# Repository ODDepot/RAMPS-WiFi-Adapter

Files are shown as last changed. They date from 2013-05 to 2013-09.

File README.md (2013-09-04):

The RAMPS WiFi Adapter provides wireless networking for RepRap's RAMPS (Arduino Mega Pololu Shield) controller.

### News

#### 9/4/2013
Version 0.2 has been tested and is functional. Further work on setup.ino and setup.py is needed for a friendly configuration process. Higher baudrates may be achieved but have not been fully tested.

#### 6/19/2013
Version 0.2 is ready to be ordered and tested. The LM358DMR2G is replacing the TLV2452CDGKR and voltage dividers are being added along with a pullup and pulldown resistor. The first version has some errors. Overdriving the TLV2452CDGKR inputs at 5V with 3.3V supply is not possible. Replacing it with a LM358DMR2G works, however, a pullup resistor for RESET and a pulldown resistor for GPIO9 on the RN-171 is needed whenever jumpers are not connected. Besides these issues, Version 0.1 is able to connect and send data. The antenna appears very capable.

#### 5/13/2013
Boards for the first version have been ordered and testing will begin soon.

### Setup

#### Using Marlin firmware and Pronterface host software
Make sure the RAMPS WiFi Adapter is installed correctly on RAMPS and the Reset and Default pin jumpers are in place. Upload setup.ino to the Arduino Mega with your custom settings. Observe output from the RN171 (WiFi module onboard the adapter) with the Arduino IDE Serial Monitor. If the RN171 successful assoicates with your wireless network, the RN171 should provide an IP Address and the only LED blinking should be green. Verify this by checking your router. Also, you may want to configure your router for Static DHCP so that it always leases the same IP Address for the same MAC Address (on the RN171).

In Configuration.h of Marlin, change '#define SERIAL_PORT 0' to '#define SERIAL_PORT 2' and change '#define BAUDRATE 250000' to '#define BAUDRATE 9600', then upload. Remove the Reset and Default pin jumpers and reset RAMPS. Wait a few seconds. In Pronterface, type [IP Address]:2000 into the 'Port' bar (for example, 192.168.1.100:2000), then connect.

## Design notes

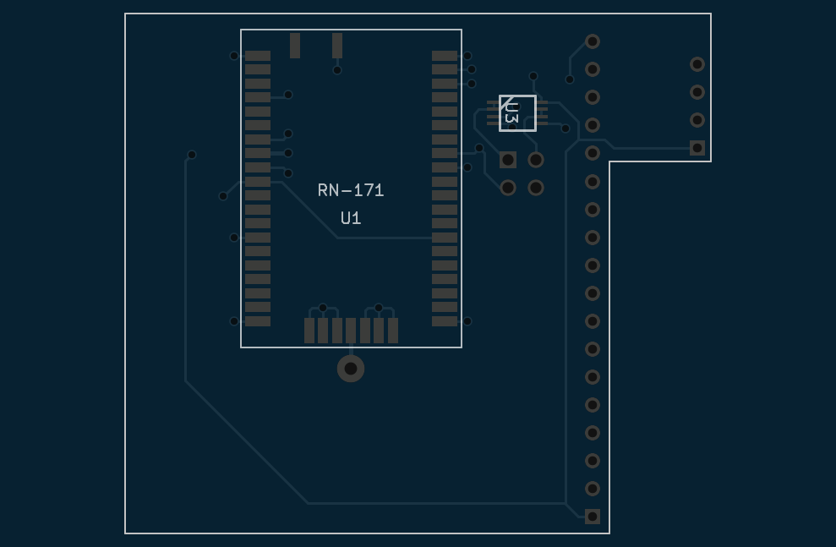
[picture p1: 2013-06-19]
rev-0.2/back.png

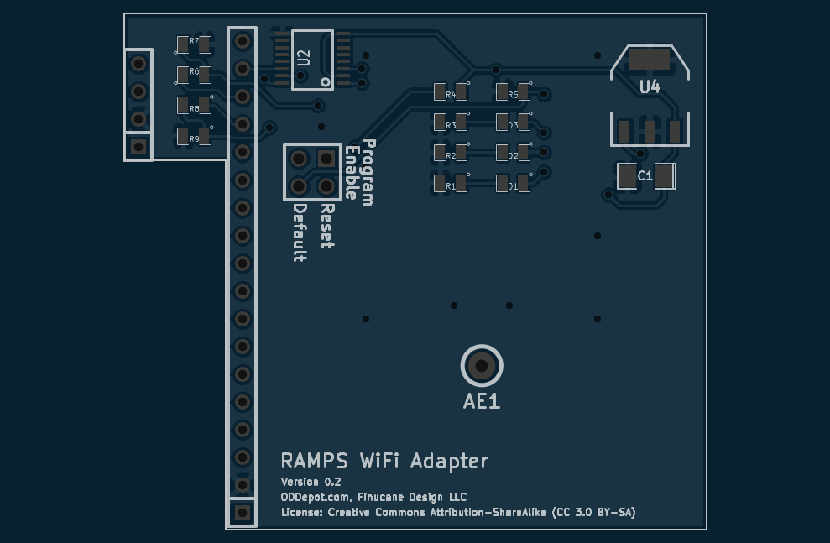
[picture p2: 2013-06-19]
rev-0.2/front.png

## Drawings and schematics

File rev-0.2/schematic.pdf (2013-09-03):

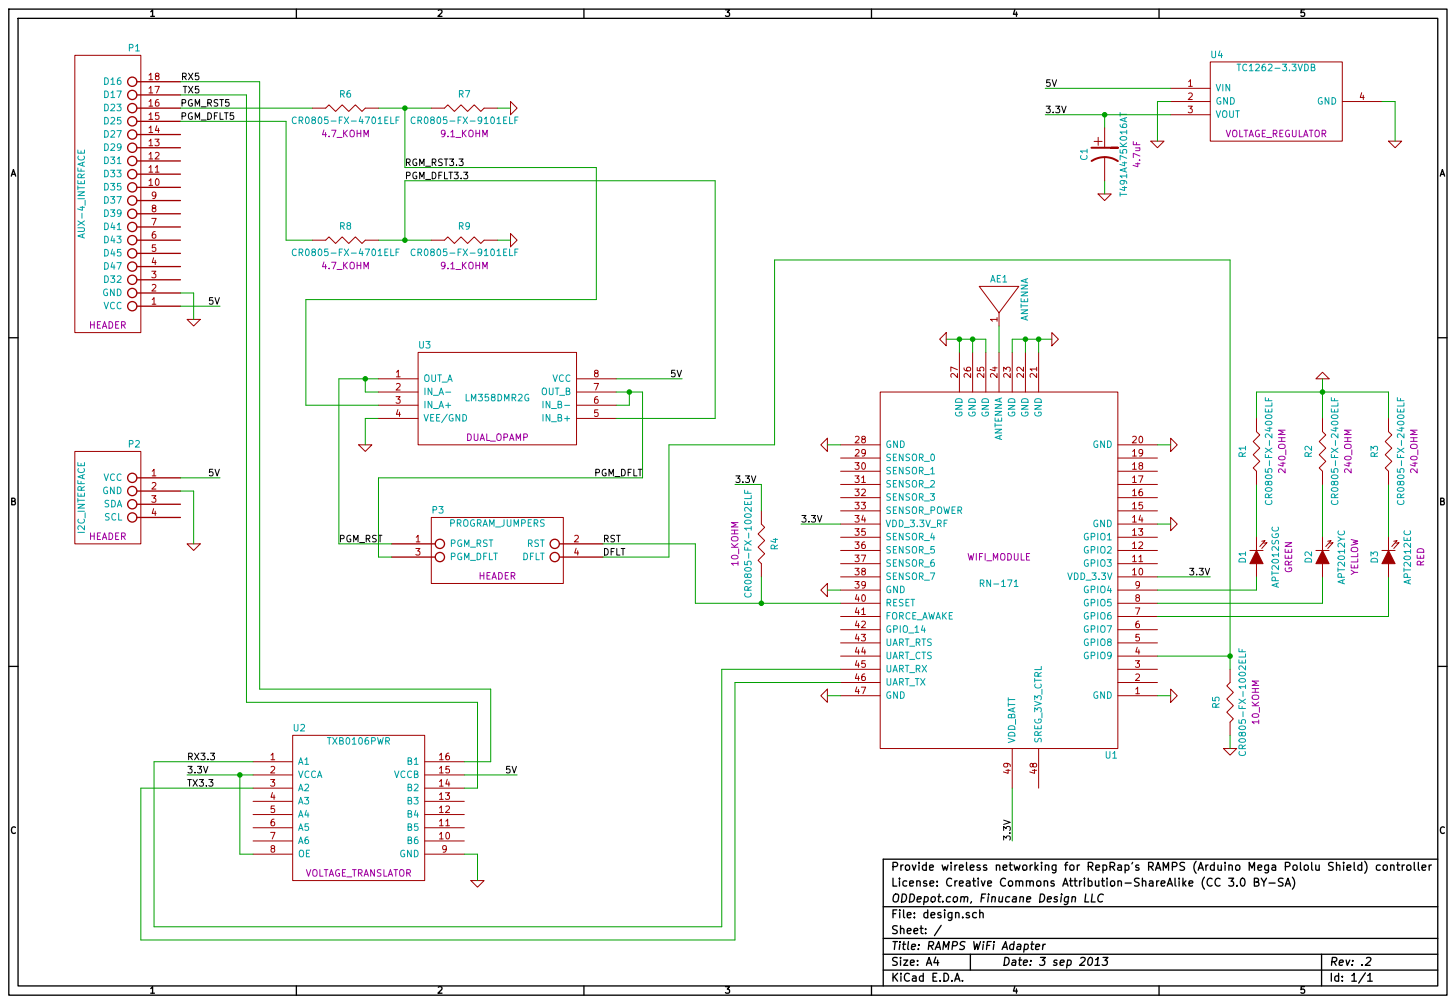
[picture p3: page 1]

Provide wireless networking for RepRap's RAMPS (Arduino Mega Pololu Shield) controller
License: Creative Commons Attribution-ShareAlike (CC 3.0 BY-SA)
ODDepot.com, Finucane Design LLC
File: design.sch
Sheet: /
Title: RAMPS WiFi Adapter
KiCad E.D.A.

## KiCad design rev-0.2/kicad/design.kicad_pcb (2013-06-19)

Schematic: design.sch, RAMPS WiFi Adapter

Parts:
AE1: ANTENNA
C1: T491A475K016AT
D1: APT2012SGC
D2: APT2012YC
D3: APT2012EC
P1: AUX-4_INTERFACE
P2: I2C_INTERFACE
P3: PROGRAM_JUMPERS
R1, R2, R3: CR0805-FX-2400ELF
R4, R5: CR0805-FX-1002ELF
R6, R8: CR0805-FX-4702ELF
R7, R9: CR0805-FX-9102ELF
U1: RN-171
U2: TXB0106PWR
U3: LM358DMR2G
U4: TC1262-3.3VDB

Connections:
/3.3V: C1.1, R4.1, U1.10 (VDD_3.3V), U1.34 (VDD_3.3V_RF), U1.49 (VDD_BATT), U2.2 (VCCA), U2.8 (OE), U4.3 (VOUT)
/5V: P1.1, P2.1, U2.15 (VCCB), U3.8 (VCC), U4.1 (VIN)
/DFLT: P3.4 (DFLT), R5.1, U1.4 (GPIO9)
/PGM_DFLT: P3.3 (PGM_DFLT), U3.6 (IN_B-), U3.7 (OUT_B)
/PGM_DFLT3.3: R8.2, R9.1, U3.5 (IN_B+)
/PGM_DFLT5: P1.15, R8.1
/PGM_RST: P3.1 (PGM_RST), U3.1 (OUT_A), U3.2 (IN_A-)
/PGM_RST5: P1.16, R6.1
/RGM_RST3.3: R6.2, R7.1, U3.3 (IN_A+)
/RST: P3.2 (RST), R4.2, U1.40 (RESET)
/RX3.3: U1.45 (UART_RX), U2.1 (A1)
/RX5: P1.18, U2.16 (B1)
/TX3.3: U1.46 (UART_TX), U2.3 (A2)
/TX5: P1.17, U2.14 (B2)
GND: C1.2, P1.2, P2.2, R1.2, R2.2, R3.2, R5.2, R7.2, R9.2, U1.1 (GND), U1.14 (GND), U1.20 (GND), U1.21 (GND), U1.22 (GND), U1.23 (GND), U1.25 (GND), U1.26 (GND), U1.27 (GND), U1.28 (GND), U1.39 (GND), U1.47 (GND), U2.9 (GND), U3.4 (VEE/GND), U4.2 (GND), U4.4 (GND)
unnamed: D1.1 (AN), U1.9 (GPIO4)
unnamed: D3.2 (CA), R3.1
unnamed: D2.2 (CA), R2.1
unnamed: D1.2 (CA), R1.1
unnamed: D3.1 (AN), U1.7 (GPIO6)
unnamed: AE1.1, U1.24 (ANTENNA)
unnamed: D2.1 (AN), U1.8 (GPIO5)

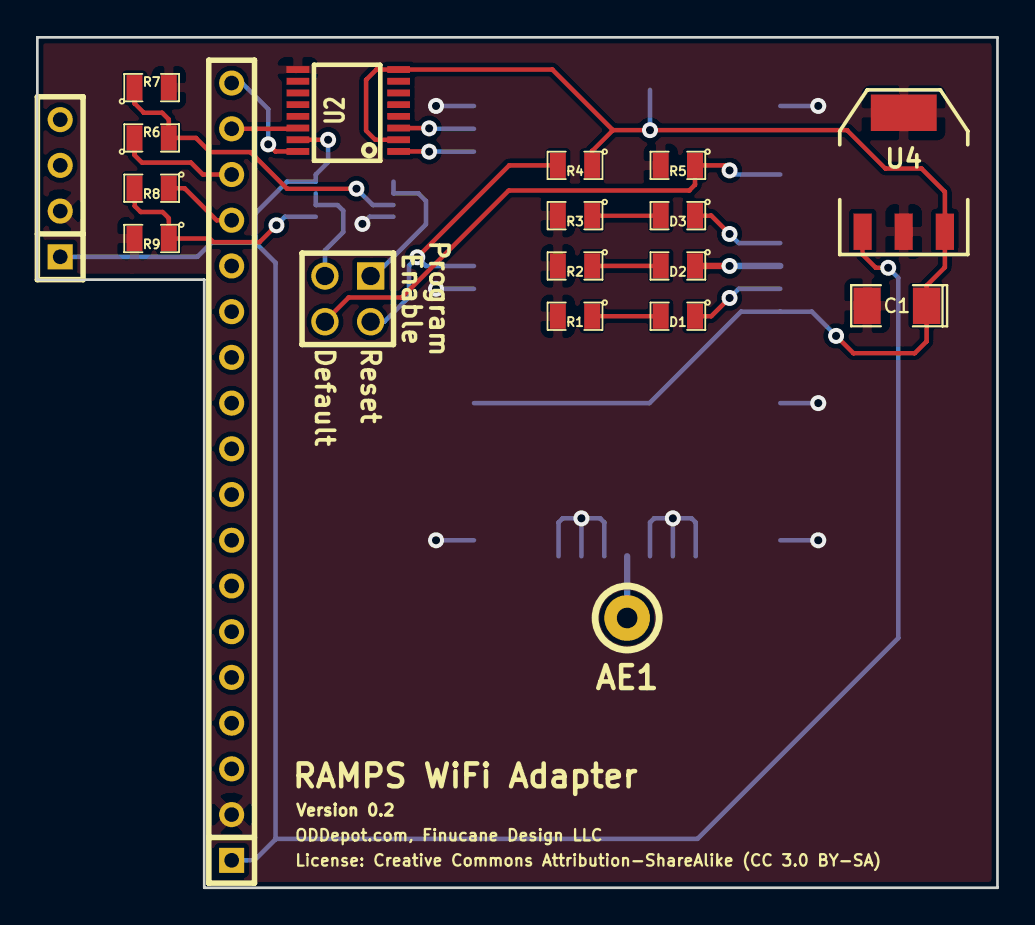
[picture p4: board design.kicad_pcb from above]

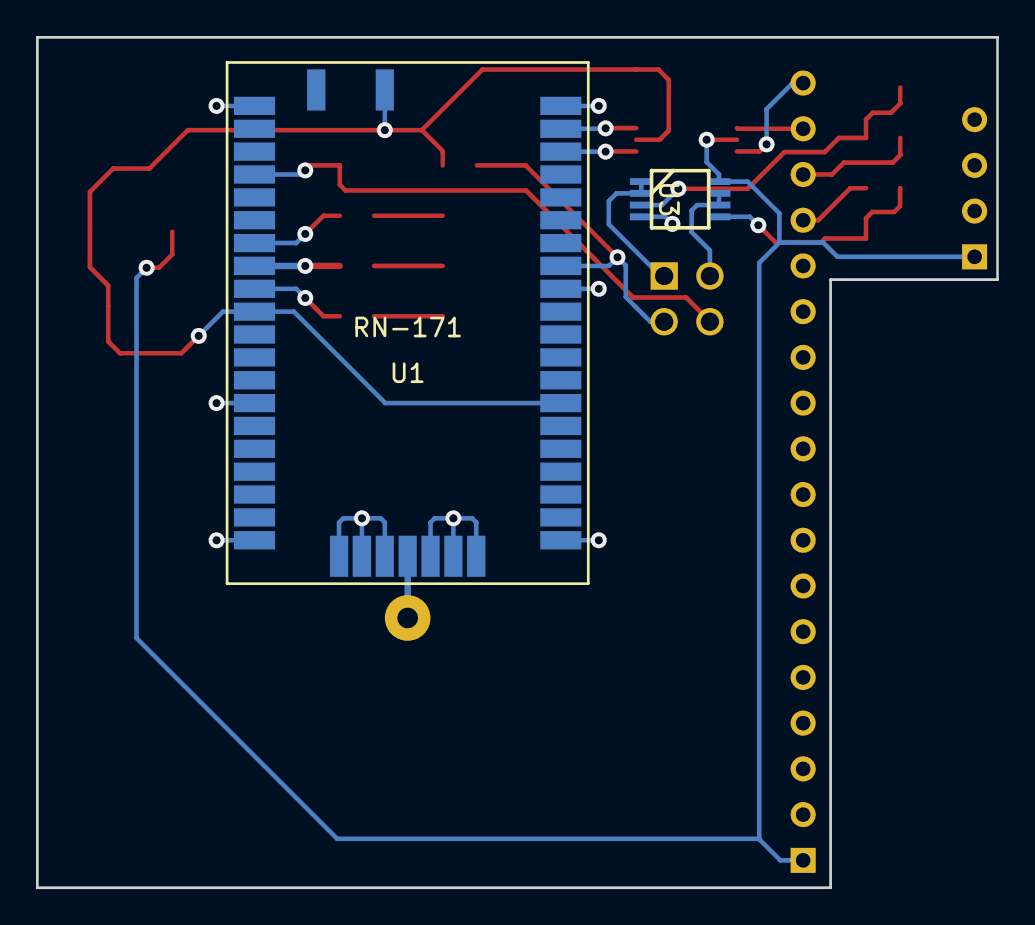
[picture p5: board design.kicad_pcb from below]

Board: 2 copper layers, 53.3 x 47.2 mm, 21 parts (2 on the bottom side), 22 nets.

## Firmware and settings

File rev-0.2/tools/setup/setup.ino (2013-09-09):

// This sketch configures the RN171 on the RAMPS WiFi Adapter. If successful, the RN171 will
// associate with your wireless network. Use the Arduino IDE Serial Monitor to observe output.
// Modify the following settings for your router. Make sure the Reset and Default pin jumpers are
// in place!

//////////////////////////////////////////////////
// Modify these settings to connect to your router
// Make sure they are exact! Double check!
//////////////////////////////////////////////////

// Type your router name here
String SSID = "My_SSID";

// Type your passphrase here
String Passphrase = "My_Passphrase";

// Uncomment ONE of the following security types...
//int Auth_Type = 0; // Open
int Auth_Type = 2; // WPA2
//int Auth_Type = 3; // WPA1
//int Auth_Type = 4; // Mixed

//////////////////////////////////////////////////
//////////////////////////////////////////////////
//////////////////////////////////////////////////

// Configuration settings for the RN171
long baud_rate = 115200;  // The baud rate between the RN171 and Mega, this must match the baud rate set in Marlin
String device_id = "RAMPS WiFi Adapter";  // If using more than one adapter, each device_id should be unique

int RST = 23;
int DFLT = 25;

const int command_buffer_size = 64;
char command[command_buffer_size];


void establish_comm() {
  Serial.begin(9600);
  Serial2.begin(9600);
}

void send_command(String str_command) {
  if (str_command != "$$$") {
      str_command += "\r\n";
  }
  str_command.toCharArray(command, command_buffer_size);
  Serial2.write(command);
}

void print_response() {
  delay(1000);
  while (Serial2.available() > 0) {
    Serial.write(Serial2.read());
  }
  Serial.write("\r\n");
}

void clear_receive_buffer() {
  delay(1000);
  while (Serial2.available() > 0) {
    Serial2.read();
  }
}

String escape_space(String string) {

  string.replace(" ", "$");
  return string;
}

void setup() {
  pinMode(RST, OUTPUT);
  pinMode(DFLT, OUTPUT);

  // The following write sequence restores the RN171 to factory defaults
  digitalWrite(DFLT, HIGH);
  delay(1000);
  digitalWrite(RST, LOW);
  delay(1000);
  digitalWrite(RST, HIGH);
  delay(1000);
  digitalWrite(DFLT, LOW);
  delay(1000);
  digitalWrite(DFLT, HIGH);
  delay(1000);
  digitalWrite(DFLT, LOW);
  delay(1000);
  digitalWrite(DFLT, HIGH);
  delay(1000);
  digitalWrite(DFLT, LOW);
  delay(1000);
  digitalWrite(DFLT, HIGH);
  delay(1000);
  digitalWrite(DFLT, LOW);
  delay(1000);
  digitalWrite(DFLT, HIGH);
  delay(1000);
  digitalWrite(DFLT, LOW);
  delay(1000);
  digitalWrite(DFLT, HIGH);
  delay(1000);
  digitalWrite(DFLT, LOW);
  delay(1000);

  // Reset the RN171
  digitalWrite(RST, LOW);
  delay(1000);
  digitalWrite(RST, HIGH);
  delay(1000);

  establish_comm();

  send_command("$$$");
  print_response();

  send_command("");  // A "hiccup" sometimes returns an error for the first commmand after "$$$", so send this and ignore response
  clear_receive_buffer();

  send_command(String(("set option device_id ") + escape_space(device_id)));
  print_response();
  
  send_command((String("set wlan ssid ") + escape_space(SSID)));
  print_response();

  send_command((String("set wlan auth ") + Auth_Type));
  print_response();

  send_command((String("set wlan phrase ") + escape_space(Passphrase)));
  print_response();

  send_command("set wlan linkmon 0");  // WiFly de-authenticates and re-authenticates continously with the AP when this is > 0, not sure why...
  print_response();
  
  send_command("set wlan join 1");
  print_response();
  
  send_command("set ip dhcp 1");
  print_response();

  send_command((String("set uart baud ") + baud_rate));
  print_response();

  send_command("save");
  print_response();
  
  // Reset the RN171 again
  digitalWrite(RST, LOW);
  delay(1000);
  digitalWrite(RST, HIGH);
  delay(1000);
}

void loop() {
}

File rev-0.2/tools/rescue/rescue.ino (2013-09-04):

// This sketch restores the RN171 on the RAMPS WiFi Adapter to factory defaults. Try this if the
// RN171 becomes unresponsive, then use debug.ino. Make sure the Reset and Default pin jumpers
// are in place! See the RN171-EK datasheet for "factory reset" sequence
// (http://www.rovingnetworks.com/resources/download/147/RN_171_EK_Data_Sheet).


int RST = 23;
int DFLT = 25;


void setup() {
  pinMode(RST, OUTPUT);
  pinMode(DFLT, OUTPUT);

  // The following write sequence restores the RN171 to factory defaults
  // Make sure the Reset and Default pin jumpers are in place!
  digitalWrite(DFLT, HIGH);
  delay(1000);
  digitalWrite(RST, LOW);
  delay(1000);
  digitalWrite(RST, HIGH);
  delay(1000);
  digitalWrite(DFLT, LOW);
  delay(1000);
  digitalWrite(DFLT, HIGH);
  delay(1000);
  digitalWrite(DFLT, LOW);
  delay(1000);
  digitalWrite(DFLT, HIGH);
  delay(1000);
  digitalWrite(DFLT, LOW);
  delay(1000);
  digitalWrite(DFLT, HIGH);
  delay(1000);
  digitalWrite(DFLT, LOW);
  delay(1000);
  digitalWrite(DFLT, HIGH);
  delay(1000);
  digitalWrite(DFLT, LOW);
  delay(1000);
  digitalWrite(DFLT, HIGH);
  delay(1000);
  digitalWrite(DFLT, LOW);
}

void loop() {
}

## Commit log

2013-05-13 Intial commit for rev-0.1, README.md, and LICENSE.md
    [design.kicad_pcb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]
2013-05-14 Create Mouser BOM
    [mouser_bom.csv]
2013-06-07 Generate solder paste gerber files
    [design-B_Paste.gbp, design-F_Paste.gtp]
2013-06-19 Adding rev-0.2 which corrects some errors with rev-0.1 (see README). Also adding some some tools (still a work in progress) for configuring the RN-171.
    [design-B_Cu.gbl, design-B_Mask.gbs, design-B_Paste.gbp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]
2013-09-03 Changing R6,R8 to 4.7KOhm and R7,R9 to 9.1KOhm. Removing unused libraries from Eeschema. Updating and fixing some errors in BOM.
    [design.sch, mouser_bom.csv]
2013-09-04 Adding setup.ino as the main method for configuration, debug.ino for serial communication and manual configuration, and rescue.ino for a factory reset procedure. Fixing issues with comm.py and setup.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
    [comm.py, rescue.ino, setup.ino]
2013-09-09 Modifying send_command() to append "\r\n", removing broken code in loop(), allowing configuration of baud rate, and cleaning up some comments.
    [setup.ino]
